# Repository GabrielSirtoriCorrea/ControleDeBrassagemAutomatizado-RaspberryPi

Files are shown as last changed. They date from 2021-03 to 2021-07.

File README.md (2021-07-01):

# Controle de Brassagem Automatizado

O Controle de Brassagem Automatizado, é um projeto desenvolvido com o objetivo de facilitar o processo de brassagem na produção de cerveja artesanal, deixando o procedimento mais automático e simples para o usuário.

## Processo de fabricação da cerveja artesanal

Antes de entendermos o funcionamento do projeto, precisamos estudar um pouco sobre as etapas do processo de fabricação de uma cerveja artesanal, e entender como cada um deles funciona.

Existem várias formas de se fazer cerveja artesanal, mas como todo alimento ou bebida, para sua produção são necessários alguns ingredientes principais:

- Malte
- Água
- Lúpulo
- Levedura

Eles são misturados de acordo com algumas etapas que podem ser entendidas pelo fluxograma abaixo:

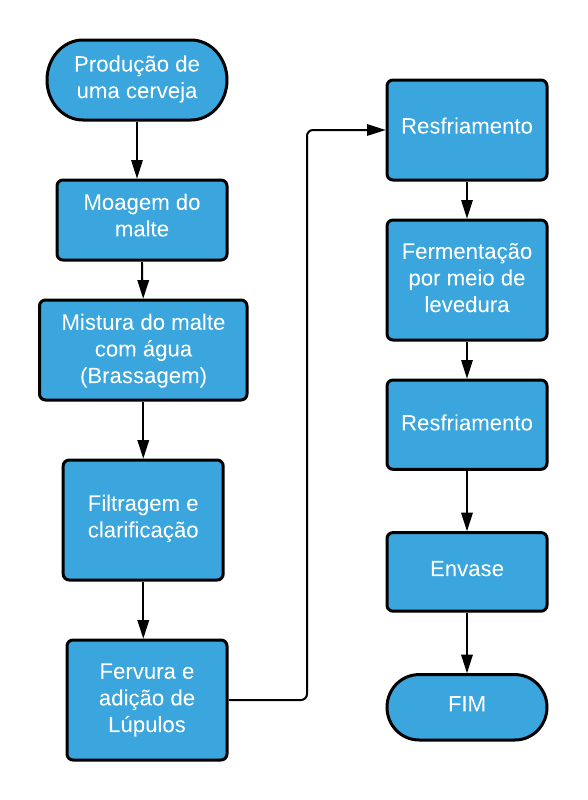
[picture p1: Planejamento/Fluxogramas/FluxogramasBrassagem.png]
Fluxograma Fabricação de cerveja
    
    
Pelo fato da fabricação da cerveja ter vários processos, nesse projeto vamos automatizar apenas 3 deles, sendo:

- Brassagem
- Filtragem e clarificação
- Fervura

Tendo isso em mente, podemos estudar um pouco mais afundo, e ver como funciona esses 3 processos de uma forma um pouco mais detalhada.

### Brassagem 

O processo de brassagem, ocorre logo após a moagem do malte, e consiste em adicionar o malte moído em uma panela de água com temperatura regulada, esse processo pode levar de 60 a 90 minutos para ser concluído, e pode ocorrer com rampas de temperatura (processo na qual o tanque mantém a temperatura em um valor determinado pelo usuário) em alguns intervalos de tempo. O fluxograma abaixo nos ajuda a compreender melhor o funcionamento desse processo:

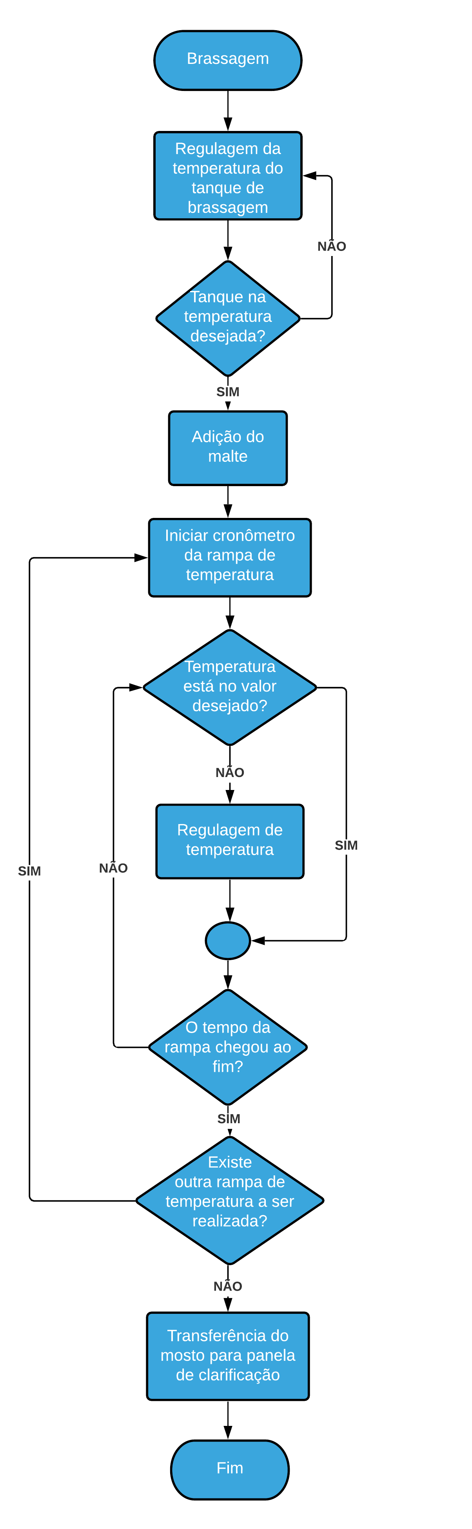
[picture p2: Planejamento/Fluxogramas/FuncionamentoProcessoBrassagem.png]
Fluxograma brassagem


### Filtragem e Clarificação

Nesse processo, o mosto (Resultado da mistura entre água e malte) é passado para uma outra panela, e começa a circular por um filtro, que será responsável por retirar as cascas dos grãos que ficaram no mosto, isso deixará a cerveja com uma coloração mais agradável e sem partículas grandes que não foram dissolvidas.

### Fervura

Após a filtragem e clarificação, entramos na etapa de fervura, essa etapa se baseia em elevar a temperatura do mosto e adicionar os Lúpulos em  alguns intervalos de tempo. Finalizada essa etapa, o mosto é levado para o processo de fermentação, o fluxograma a seguir mostra essa etapa de forma detalhada:

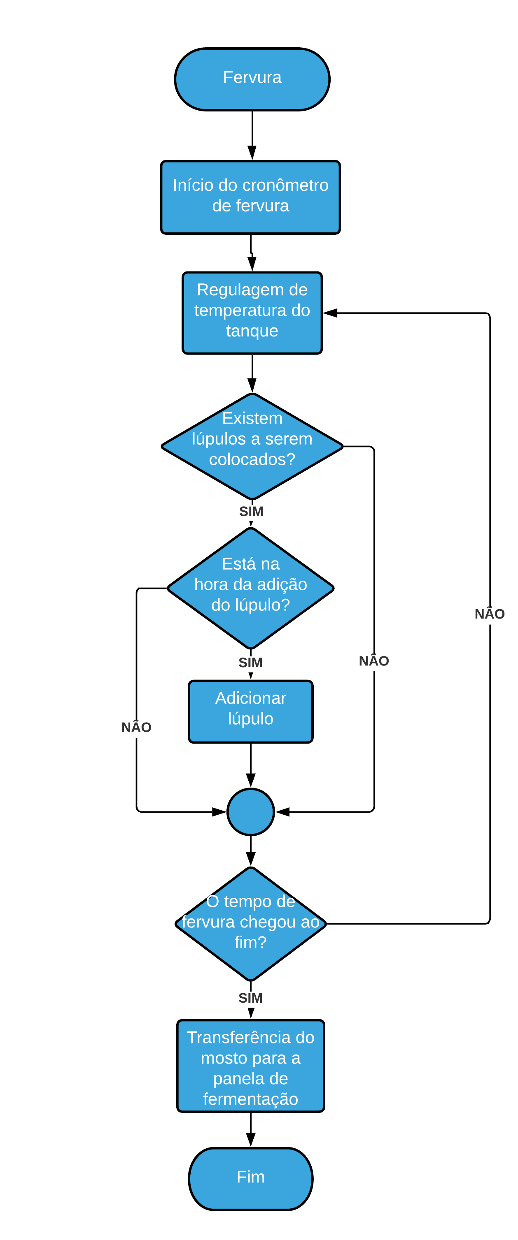
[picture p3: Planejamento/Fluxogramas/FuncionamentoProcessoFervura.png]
Fluxograma fervura


Com todos as etapas já compreendidas, podemos fazer um fluxograma completo, com todos os processos envolvidos.

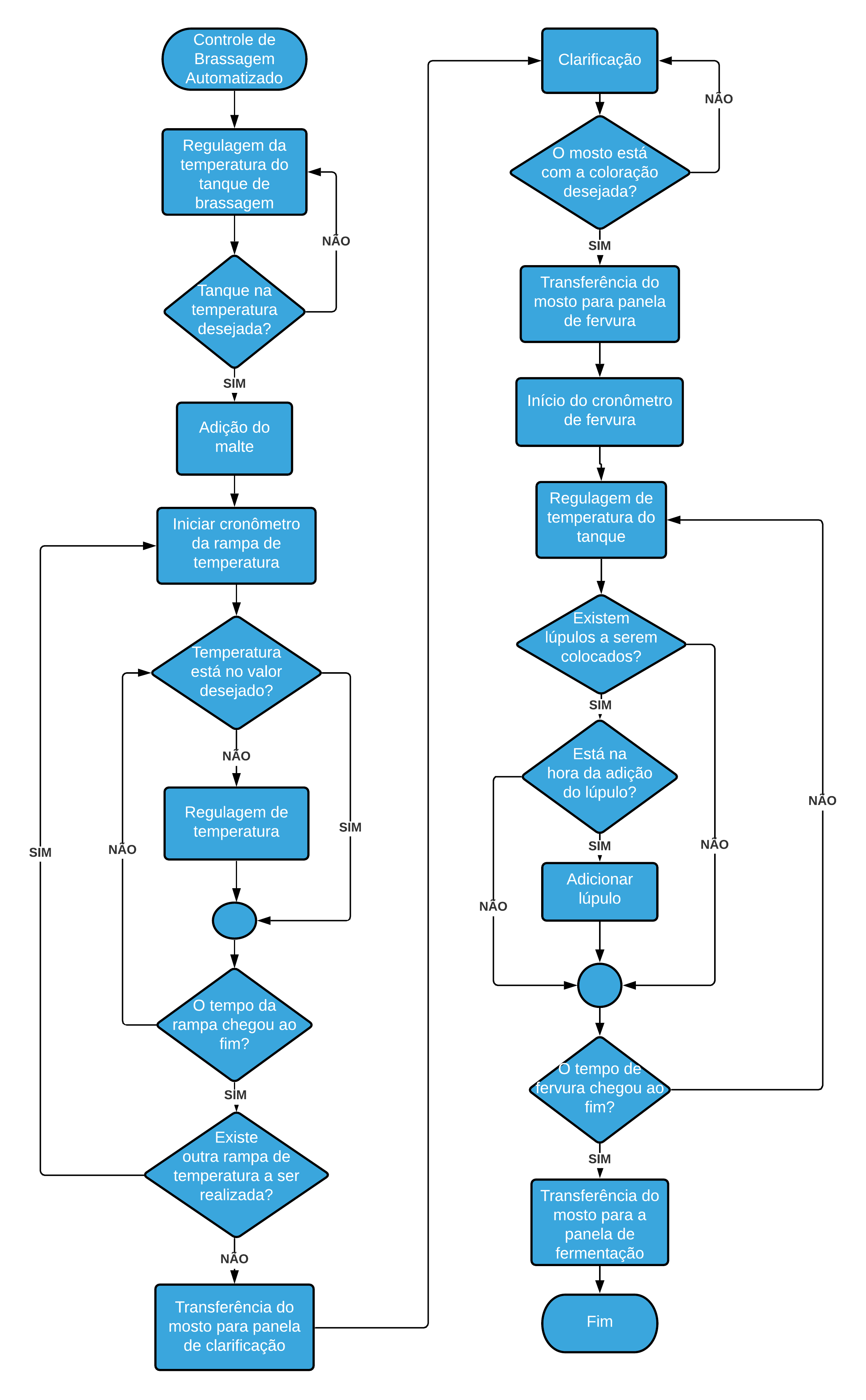
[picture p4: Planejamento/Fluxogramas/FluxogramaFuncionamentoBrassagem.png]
Fluxograma completo


Agora que conhecemos os 3 processos que serão automatizados, podemos criar uma lógica para o controle dos mesmos. Analisando as 3 etapas, podemos concluir que a principal variável existente nesses processos é a **TEMPERATURA**, que deve ser controlada na **BRASSAGEM** e **FERVURA**. Sendo assim, precisamos criar alguma estratégia para que possamos manter a **TEMPERATURA** sempre no valor que desejarmos.

## Variáveis de processo

### Controle de temperatura

A lógica de controle de temperatura consiste básicamente em 3 elementos:

- Sensor: Responsável por ler a temperatura atual do tanque
- Controlador: Responsável por receber o valor da temperatura do sensor, compará-la com o valor desejado e enviar um comando para o atuador
- Atuador: Recebe o comando do controlador, e age físicamente no processo, modificando sua temperatura

Tendo isso em mente, os dispositivos escolhidos para realizar essas funções foram:

- Sensor (TT): Sensor de temperatura DS18B20
- Controlador (TIC): Raspberry Pi com módulo ControlBeer
- Atuador (Resistência): Resistência elétrica para panela
- Relé (TY): Necessário para o acionamento da resistência

Com todos os instrumentos escolhidos, podemos criar um diagrama para auxiliar na visualização da lógica de controle de temperatura:

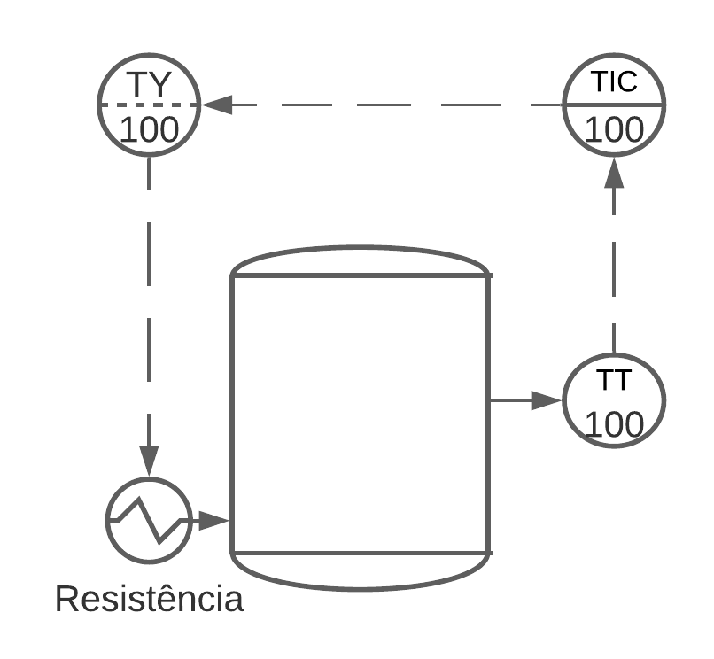
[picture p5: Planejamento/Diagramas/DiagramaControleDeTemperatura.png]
Diagrama de controle de temperatura
  

Diferentemente dos processos de brassagem e fervura, a **FILTRAGEM E CLARIFICAÇÃO**, não depende de um controle de temperatura do líquido na panela, mas sim, do seu fluxo na passagem pelo filtro, sendo assim, precisamos criar outra estratégia para que possamos transitar o mosto entre as panelas, e para realizar a passagem do líquido pelo filtro.

### Fluxo do líquido

Para realizarmos o fluxo do líquido entre as panelas, precisamos de mais alguns instrumentos, sendo eles:

- Motor: Auxilia a manter o mosto em movimento dentro da panela
- Bomba: Responsável por realizar o fluxo do líquido entre as panelas e atravéz do filtro
- Visor de vazão (FV): Necessário para analisarmos a coloração do mosto
- Válvulas de acionamento manual: Necessária para controlar o fluxo do mosto entre as panelas 

Dessa forma, o controle de fluxo do projeto será feito de acordo com o diagrama:

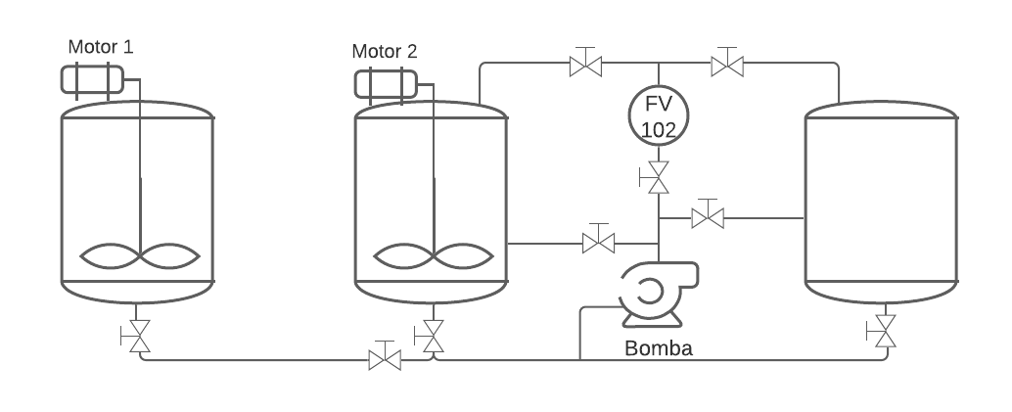
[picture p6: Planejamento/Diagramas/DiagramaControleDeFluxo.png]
Diagrama de controle de fluxo


É importante ressaltar que, devido a grande quantidade de válvulas, não é possível controla-lás eletricamente por meio de um solenoide, pois não teriamos um controlador com a quantidade de saídas necessárias, por conta disso, o usuário terá de fazer esse controle manualmente.

Agora que sabemos como será o controle das váriaveis e todos os instrumentos que iremos utilizar, podemos juntar os dois diagramas criados anteriormente e criar um diagrama final do projeto.

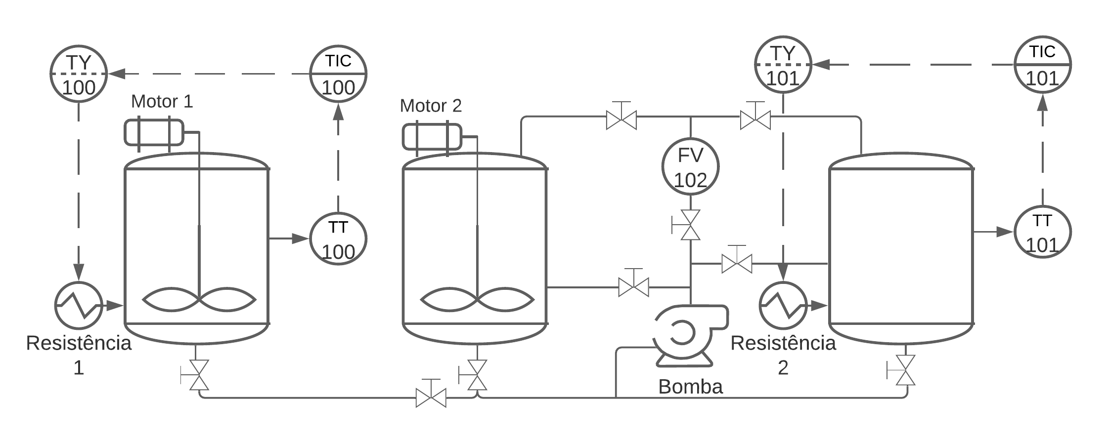
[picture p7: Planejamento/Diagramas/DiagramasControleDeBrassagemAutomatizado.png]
Diagrama final


## Componentes e ligações eletrônicas

Após identificarmos todos os instrumentos que iremos utilizar, precisamos de alguns componentes eletrônicos para que possamos acioná-los e controlá-los, sendo eles:

- Fonte 12V
- Módulo regulador de tensão 12V-5V LM2596
- Raspberry Pi 3 Model B
- 2x Sensores de temperatura DS18B20 
- 2x Resistores 4.7K Ohms
- 5x Módulos Relés
- Display Touch Nextion HDMI 1024x600

Tendo todos os componentes em mãos, podemos fazer as seguintes ligações:

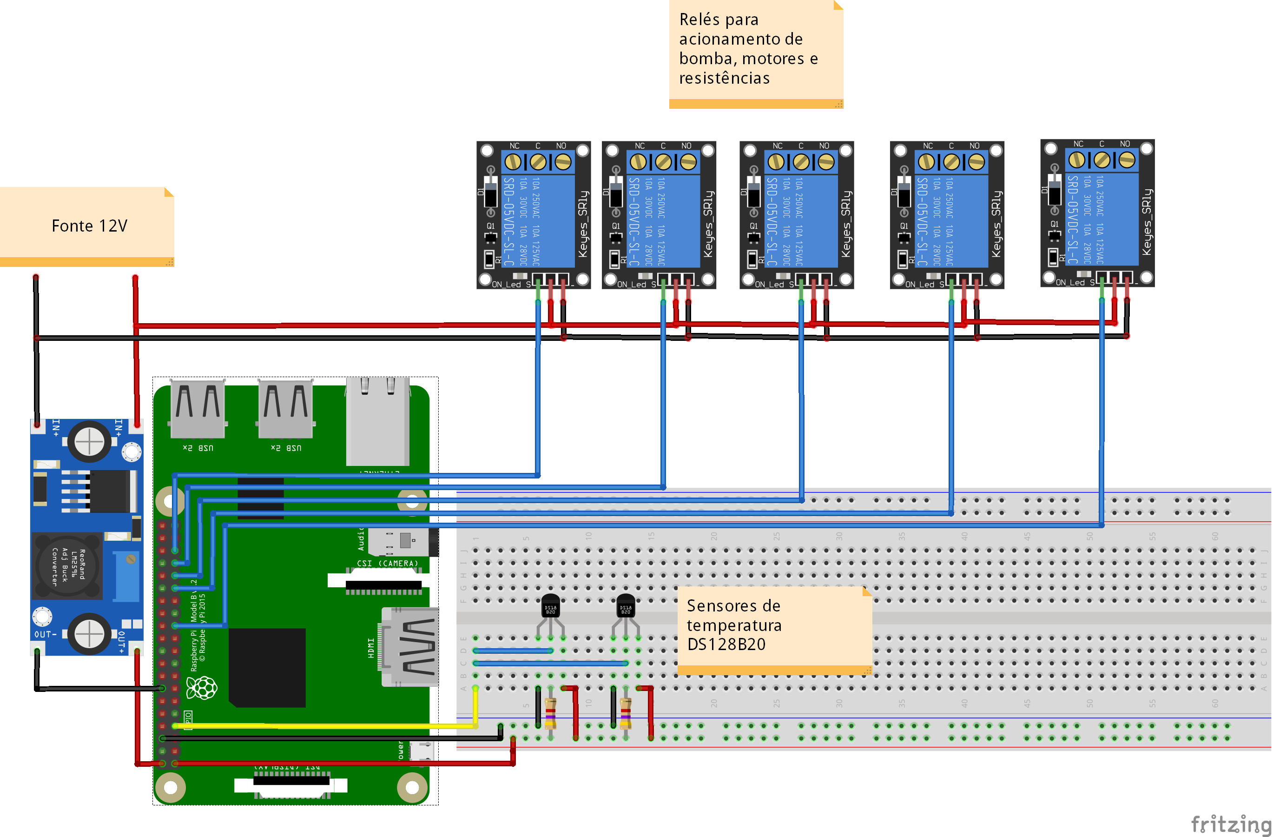
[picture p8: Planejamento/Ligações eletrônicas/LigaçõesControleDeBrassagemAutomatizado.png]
Esquema de ligações


Apesar do esquema acima ser bem simples, ele não foi utilizado no projeto, em seu lugar, foi utilizado um módulo Raspberry Pi chamado de Control Beer Pi.

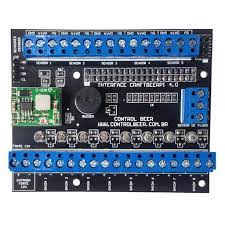
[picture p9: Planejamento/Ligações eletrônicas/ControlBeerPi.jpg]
Control Beer Pi


Esse módulo já é bem conhecido pelos cervejeiros, e nos auxilia muito por já conter um regulador de tensão 12V-5V, os resistores de 4.7k Ohms e borns para conexão, dessa forma, não precisamos de uma protoboard para fazermos a conexão.

O display nextion será a IHM do projeto, e será conectado diretamente ao Raspberry Pi por um cabo HDMI, e alimentado por um cabo USB, conectado também ao Raspberry.

## Lógica do projeto

Agora que sabemos todos os componentes que iremos utilizar, precisamos criar uma lógica para controlar todo o projeto. Para esse projeto, separamos a lógica em 3 núcleos:

- Interface: É responsável pela interação com o usuário, será exibida no IHM Nextion
- Scripts: São responsáveis pela lógica de controle de todo o sistema
- Status: Estruturado no formato JSON, é o arquivo que irá conter os estados de todos os componentes do sistema, e as configurações realizadas pelo usuário

### Interface

A Interface do projeto foi criada com a linguagem **JAVA**, juntamente com o pacote **SWING** para a criação dos Layouts. Com esse pacote importado, as classes Java podem ter um layout, dessa forma, podemos mudar o Layout da Interface apenas chamando uma outra classe. Nesse projeto, temos 4 classes Java, sendo elas:

- Interface.java: Tela inicial do sistema
- StatusController.java: Contém métodos para leitura do arquivo Status.json
- TelaBrassagemManual.java: Tela para brassagem de modo manual
- TelaNovaBrassagem.java: Tela de configuração de uma nova brassagem

#### StatusController.java

A classe StatusController é uma classe simples Java sendo a única no projeto que não utiliza o pacote Swing. Ela é responsável por **Ler e Escrever** no arquivo **Status.json**, através dos métodos **readStatus()**, **writeStatus()** e **resetStatus()**, podemos fazer isso a partir do pacote **org.json**, que foi importado para o projeto. A estrutura do arquivo **Status.json** foi criada da seguinte forma:

```
{
    "BrewStatus":"Pausado",
    "Bomb":false,
    "BrewMode":"Automatic",
    "Tank1":{
        "Ramps":[[0,0],[0,0]],
        "MaltAlert":false,
        "Temperature":0,
        "Motor":false,
        "NextProcess":false,
        "SetPoint":0,
        "ActualRamp":0,
        "Resistence":false
        },
    "Tank2":{
        "ClarificationTime":0,
        "Motor":false,
        "NextProcess":false
        },
    "Tank3":{
        "Temperature":0,
        "NextProcess":false,
        "Hops":[0,0,0],
        "BoilTime":0,
        "SetPoint":0,
        "Resistence":false,
        "HopAlert":false
        }
}
```

A implementação do método **readStatus()** é simples, só precisamos ler o arquivo Status.json com a classe **FileReader** do pocote java.io, converter para um tipo JSONObject, armazenar em uma variável e retorná-la. Essa implementação foi feita dentro de um LOOP while, isso nos permite fazer uma verificação de se a variável retornada está vazia, se ela estiver, acontece novamente a leitura. Esse tipo de erro pode ocorrer quando os scripts estiverem manipulando os dados do arquivo, dessa forma, o JSONObject não será retornado vazio, evitando um erro em outra parte do sistema.

```
public static JSONObject readStatus(){
    do{
        try {
            jsonParser = new JSONParser();
            jsonObject = new JSONObject(jsonParser.parse(new FileReader("../status.json")).toString());
        } catch (ParseException | IOException | NullPointerException e) {
            e.printStackTrace();
        }
    }while(jsonObject.isEmpty());
            
    return jsonObject;
    }
```

O método **writeStatus()** foi implementado da seguinte forma, primeiro, utilizamos o método **readStatus()** da própria classe para lermos os estados atuais de Status.json e armazená-los em uma variável do tipo JSONObject, podendo assim manipular o JSON através do método **put()**. Após isso, criamos um objeto da classe **FileWriter**, contida no pacote java.io, e escrevemos o JSONObject no arquivo Status.json, através do método **write()**. É importante ressaltar também que foi utilizado um polimorfismo em **writeStatus()**, para que possamos escrever no JSON um objeto qualquer ou um JSONArray. Além disso, colocamos uma verificação do parâmetro tank em ambos os métodos, isso nos permite mudar as variáveis de um tanque, ou do projeto como um todo.

```
public static void writeStatus(String  tank, String target, Object value){
    try {
        if(tank != null){
            originalJson = readStatus();
            jsonObject = readStatus().getJSONObject(tank);
            jsonObject.put(target, value);
            originalJson.put(tank, jsonObject);
            System.out.println(jsonObject);
            writer = new FileWriter("../status.json");
                
            writer.write(originalJson.toString());
        }else{
            jsonObject = readStatus();
            writer = new FileWriter("../status.json");
            System.out.println(jsonObject);
            jsonObject.put(target, value);
            writer.write(jsonObject.toString());
        }
            
        writer.close();
    } catch (IOException ex) {
       ex.printStackTrace();
    }
}

public static void writeStatus(String  tank, String target, JSONArray value){
    try {
        if(tank != null){
            originalJson = readStatus();
            jsonObject = readStatus().getJSONObject(tank);
            jsonObject.put(target, value);
            originalJson.put(tank, jsonObject);
            System.out.println(jsonObject);
            writer = new FileWriter("../status.json");
                
            writer.write(originalJson.toString());
        }else{
            jsonObject = readStatus();
            writer = new FileWriter("../status.json");
            System.out.println(jsonObject);
            jsonObject.put(target, value);
            writer.write(jsonObject.toString());
        }
            
        writer.close();
    } catch (IOException ex) {
        ex.printStackTrace();
    }
}
```

O método **resetStatus()** também foi implementado de forma simples, apenas criamos um novo JSONObject a partir de uma String que contém todos os valores do JSON setado em 0 ou false, a partir disso, escrevemos no Arquivo utilizando o **FileWriter** novamente 

```
public static void resetStatus(){
    try { 
        jsonObject = new JSONObject("{\"BrewStatus\":\"Pausado\",\"Tank3\":{\"Temperature\":0,\"NextProcess\":false,\"Hops\":[0,0,0],\"BoilTime\":0,\"SetPoint\":0,\"Resistence\":false,\"HopAlert\":false},\"Tank2\":{\"ClarificationTime\":0,\"Motor\":false,\"NextProcess\":false},\"BrewMode\":\"Automatic\",\"Tank1\":{\"Ramps\":[[0,0],[0,0]],\"MaltAlert\":false,\"Temperature\":0,\"Motor\":false,\"NextProcess\":false,\"SetPoint\":0,\"ActualRamp\":0,\"Resistence\":false},\"Bomb\":false}");

        writer = new FileWriter("../status.json");
        writer.write(jsonObject.toString());
        writer.close();
    } catch (IOException ex) {
        Logger.getLogger(StatusController.class.getName()).log(Level.SEVERE, null, ex);
    }
        
}
```

#### Interface.java

O layout da tela inicial foi criado da seguinte forma:

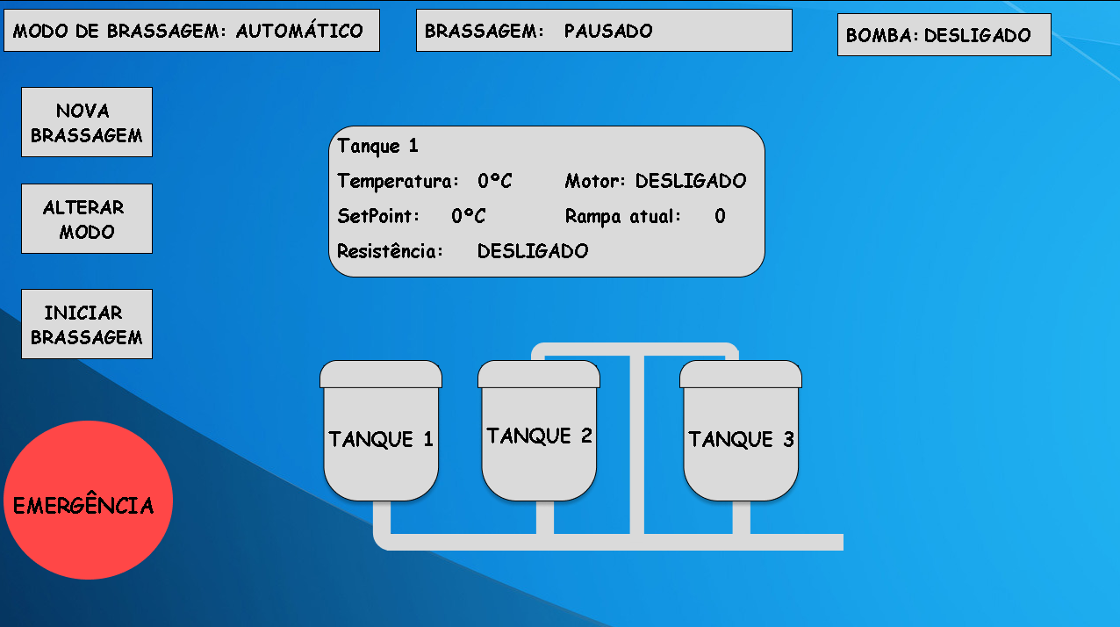
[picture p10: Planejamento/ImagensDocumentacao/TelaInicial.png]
TelaInicial


Para essa tela temos alguns componentes que são manipulados pela classe, são eles:

- Labels:

   - lblBomb: Mostra o estado da bomba
   - lblBrewStatus: Mostra o estado da brassagem (Pausado ou Em andamento)
   - lblParameter: Mostra a variável do tanque que está sendo exibida
   - lblResult: Mostra o valor da variável do tanque
   - lblStartStop: Muda o nome do botão btnStartBrew para INICIAR BRASSAGEM ou PAUSAR BRASSAGEM
   - lblTankNumber: Mostra qual é o tanque na qual as variáveis estão sendo exibidas

- Botões:

   - btnChangeMode: Chama a classe TelaBrassagemManual
   - btnEmergency: Reseta todas as variáveis do arquivo Status.json.
   - btnNewBrew: Chama a classe TelaNovaBrassagem
   - btnStartBrew: Inicia a lógica do projeto
   - btnTank1: Mostra os valores das váriaveis do tanque 1 nos labels lblResults
   - btnTank2: Mostra os valores das váriaveis do tanque 2 nos labels lblResults 
   - btnTank3: Mostra os valores das váriaveis do tanque 3 nos labels lblResults

Com todos os Botões e Labels já adicionados, precisamos implementar os métodos de cada botão para que as funções possam ser executadas quando pressionados.

Para os botões **btnChangeMode** e **btnNewBrew** foram adicionadas apenas funções que chamam uma outra classe, abaixo temos um exemplo dessa implementação:

```
private void btnNewBrewActionPerformed(java.awt.event.ActionEvent evt){                                           
    new TelaNovaBrassagem().setVisible(true);
    dispose();
    }
```

Nos botões **btnTank1**, **btnTank2**, **btnTank3** apenas mudamos o valor da variável **tankControled**, ela é responsável por armazenar o valor do tanque na qual as variáveis estão sendo exibidas na tela.

```
private void btnTank1ActionPerformed(java.awt.event.ActionEvent evt) {
    tankControled = 1;
}
```

No botão **btnEmergency**, chamamos o método **resetStatus()** da classe StatusController, dessa forma, todos os valores contidos em Status.json são resetados.

```
private void btnEmergencyActionPerformed(java.awt.event.ActionEvent evt){  
    new StatusController().resetStatus();
}
```

No Botão **btnStartBrew** criamos um objeto da classe StatusController e com o método **writeStatus()** mudamos o valor da váriavel **BrewStatus**, contida no em Status.json, para EM ANDAMENTO ou PAUSADO, isso vai depender do valor que estava contido anteriormente.

```
private void btnStartBrewActionPerformed(java.awt.event.ActionEvent evt) {                   
    status = new StatusController();
        
    if(brewStarted){
    status.writeStatus(null, "BrewStatus", "Pausado");
    lblBrewStatus.setText("PAUSADO");
    lblStartStop.setText("<html><center> INICIAR BRASSAGEM <center></html>");
    }else{
    status.writeStatus(null, "BrewStatus", "Em andamento");
    lblBrewStatus.setText("EM ANDAMENTO");
    lblStartStop.setText("<html><center> PAUSAR BRASSAGEM <center></html>");
    }
        
    brewStarted = !brewStarted;
}
```

Agora que nós ja temos todos os componentes e implementamos os métodos de todos os botões, precisamos fazer com que eles sejam atualizados constantemente, para sabermos os valores atuais das variáveis. Para isso, foi adicionada uma nova classe dentro da classe Interface.java, sendo ela a **TankController**, essa classe implementa as funções de uma interface java, chamada **ActionListener**, que foi importada para o projeto e contém o método abstrato **actionPerformed()**, esse método permite que todas as instruções contidas nele sejam executadas em LOOP, nos permitindo atualizar as variáveis em tempo real, abaixo podemos ver um exemplo para implementação da interface java **ActionListener**.

```
class TankController implements ActionListener{
    @Override
    public void actionPerformed(ActionEvent e) {
        try {

            //Instruções a serem executadas em LOOP

        } catch (InterruptedException ex) {
            Logger.getLogger(Interface.class.getName()).log(Level.SEVERE, null, ex);
        }
    } 
}
```

Podemos agora implementar a função actionPerformed() com tudo que queremos executar em loop no nosso sistema. No nosso caso, vamos fazer a verificação da variável **tankControled**, e mostrar os valores das variáveis do tanque correspondente, além de verificar as variáveis **Alert** em Status.json, para que possamos mostrar um alerta na tela, avisando ao usuário que uma etapa da produção foi finalizada.

```
class TankController implements ActionListener{
    @Override
    public void actionPerformed(ActionEvent e) {
        try {
            Thread.currentThread().sleep(1000);
            status = new StatusController();
            lblBomb.setText(booleanStatus(status.readStatus().getBoolean("Bomb")));

            if(status.readStatus().getJSONObject("Tank1").getBoolean("MaltAlert")){   //Verificação dos alertas
                JOptionPane.showMessageDialog(null, "ADICIONE O MALTE NA PANELA DE MOSTURAÇÃO!!!", "ATENÇÃO!!!", JOptionPane.WARNING_MESSAGE);
            }
            if(status.readStatus().getJSONObject("Tank3").getBoolean("HopAlert")){
                JOptionPane.showMessageDialog(null, "ADICIONE O LÚPULO NA PANELA DE FERVURA!!!", "ATENÇÃO!!!", JOptionPane.WARNING_MESSAGE);
            }
            if(status.readStatus().getJSONObject("Tank1").getBoolean("NextProcess")){
                JOptionPane.showMessageDialog(null, "ACIONE AS VÁVULAS PARA O PROCESSO DE CLARIFICAÇÃO!!!", "ATENÇÃO!!!", JOptionPane.WARNING_MESSAGE);
            }
            if(status.readStatus().getJSONObject("Tank2").getBoolean("NextProcess")){
                JOptionPane.showMessageDialog(null, "ACIONE AS VÁVULAS PARA O PROCESSO DE FERVURA!!!", "ATENÇÃO!!!", JOptionPane.WARNING_MESSAGE);
            }
            if(status.readStatus().getJSONObject("Tank3").getBoolean("NextProcess")){
                JOptionPane.showMessageDialog(null, "ACIONE AS VÁVULAS PARA O PROCESSO DE FERMENTAÇÃO!!!", "ATENÇÃO!!!", JOptionPane.WARNING_MESSAGE);
            }

            switch(tankControled){  //Verificação do tanque na qual deve exibir as variáveis 
                case 1:
                    lblTankNumber.setText("Tanque 1");

                    lblParameter1.setText("Temperatura:");
                    lblParameter2.setText("SetPoint:");
                    lblParameter3.setText("Resistência:");
                    lblParameter4.setText("Motor:");
                    lblParameter5.setText("Rampa atual:");

                    lblResult1.setText(Integer.toString(status.readStatus().getJSONObject("Tank1").getInt("Temperature")) + "ºC");
                    lblResult2.setText(Integer.toString(status.readStatus().getJSONObject("Tank1").getInt("SetPoint")) + "ºC");
                    lblResult3.setText(booleanStatus(status.readStatus().getJSONObject("Tank1").getBoolean("Resistence")));
                    lblResult4.setText(booleanStatus(status.readStatus().getJSONObject("Tank1").getBoolean("Motor")));
                     lblResult5.setText(Integer.toString(status.readStatus().getJSONObject("Tank1").getInt("ActualRamp")));
                     break;
                case 2:
                    lblTankNumber.setText("Tanque 2");

                    lblParameter1.setText("Motor:");
                    lblParameter2.setText("");
                    lblParameter3.setText("");
                    lblParameter4.setText("");
                    lblParameter5.setText("");

                    lblResult1.setText(booleanStatus(status.readStatus().getJSONObject("Tank2").getBoolean("Motor"));
                    lblResult2.setText("");
                    lblResult3.setText("");
                    lblResult4.setText("");
                    lblResult5.setText("");
                    break;
                case 3:
                    lblTankNumber.setText("Tanque 3");

                    lblParameter1.setText("Temperatura:");
                    lblParameter2.setText("SetPoint");
                    lblParameter3.setText("Resistência:");
                    lblParameter4.setText("");
                    lblParameter5.setText("");
                    lblResult1.setText(Integer.toString(status.readStatus().getJSONObject("Tank3").getInt("Temperature")) + "ºC");
                    lblResult2.setText(Integer.toString(status.readStatus().getJSONObject("Tank3").getInt("SetPoint")) + "ºC");
                    lblResult3.setText(booleanStatus(status.readStatus().getJSONObject("Tank3").getBoolean("Resistence")));
                    lblResult4.setText("");
                    lblResult5.setText("");
                    break;
            }
        } catch (InterruptedException ex) {
            Logger.getLogger(Interface.class.getName()).log(Level.SEVERE, null, ex);
        }  
    }
    private String booleanStatus(boolean status){
        if(status) return "LIGADO";
        else return "DESLIGADO";
    }
}
```

Depois de implementarmos o método, precisamos executá-lo, para isso precisamos importar a classe **Timer** do pacote Swing, e criarmos um objeto passando como parâmetro um objeto da classe **TankController**, após isso, chamamos o método **start()**.

```
Timer timer = new Timer(1000, new TankController());
timer.start();
```

#### TelaBrassagemManual.java

A TelaBrassagemManual fornece ao usuário a opção de controlar todo o sistema manualmente, seu layout foi criado da seguinte forma:

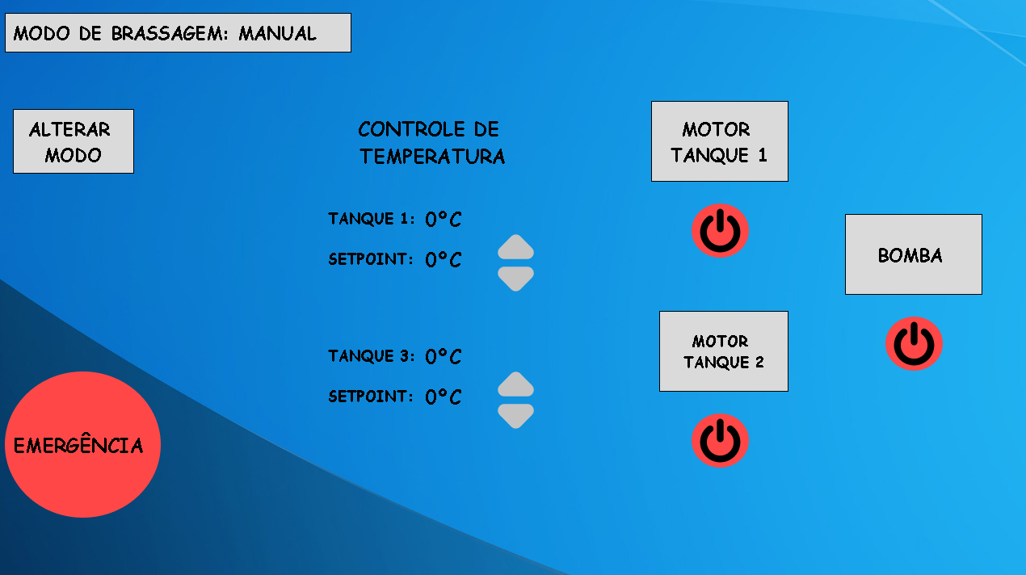
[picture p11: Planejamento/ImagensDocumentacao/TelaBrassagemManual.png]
TelaBrassagemManual


Para esse layout, temos os seguintes componentes

- Labels

    - lblSetpointTank1: Mostra o SetPoint de temperatura do tanque 1
    - lblSetPointTank3: Mostra o SetPoint de temperatura do tanque 3
    - lblTempTank1: Mostra o valor atual da temperatura do tanque 1
    - lblTempTank3: Mostra o valor atual da temperatura do tanque 3
    - ledBomb: Mostra o estado da bomba
    - ledMotorTank1: Mostra o estado do motor do tanque 1
    - ledMotorTank2: Mostra o estado do motor do tanque 2

- Botões

    - btnAdSetpointTank1: Adiciona +1 ao Setpoint de temperatura do tanque 1
    - btnAdSetpointTank3: Adiciona +1 ao Setpoint de temperatura do tanque 3
    - btnSubSetpointTank1: Subtrai -1 ao Setpoint de temperatura do tanque 1
    - btnSubSetpointTank3: Subtrai -1 ao Setpoint de temperatura do tanque 3
    - btnBomb: Muda o estado da bomba
    - btnChangeMode: Chama a classe TelaInicial
    - btnEmergency: Reseta todas as variáveis do arquivo Status.json 
    - btnMotorTank1: Muda o estado do motor do tanque 1
    - btnMotorTank2: Muda o estado do motor do tanque 2

Para a brassagem manual, os botões **btnMotorTank1**, **btnMotorTank2** e **btnBomb** tem a função de mudar as variáveis contidas em Status.json de forma direta, então criamos uma variável para armazenar o estado de cada elemento a ser controlado, pegamos esse valor e o invertemos, depois passamos como parâmetro através do método **writeStatus()**. Para o usuário ter a informação do valor da variável, foi adicionado um ícone de ON/OFF em um label vazio, a imagem a ser exibida, depende do valor da variável.

```
private void btnBombActionPerformed(java.awt.event.ActionEvent evt) {                                        
        status = new StatusController();
        bombStatus =  !bombStatus;
        status.writeStatus(null, "Bomb", bombStatus);
        if(bombStatus){
            ledBomb.setIcon(ledON);
        }else{
            ledBomb.setIcon(ledOFF);
        }
```

Os botões **btnSubSetPointTank1**, **btnSubSetPointTank3**, **btnAdSetPointTank1** e **btnAdSetPointTank3**, foram implementados com uma lógica semelhante a dos botões citados anteriormente, sua única diferença é a de adicionar +1 ou subtrair -1 ao valor lido, e mostrá-lo no label correspondente.

```
private void btnAdSetpointTank1ActionPerformed(java.awt.event.ActionEvent evt) {     
        status = new StatusController();
        Tank1SetPointValue =  Tank1SetPointValue + 1;
        status.writeStatus("Tank1", "SetPoint", Tank1SetPointValue);
        lblSetpointTank1.setText(Integer.toString(Tank1SetPointValue)+"ºC");
}
```

Para podermos atualizar constantemente o valor de temperatura dos tanques, foi utilizada a mesma lógica de Interface.java, utilizando uma classe, dessa vez a TempControl,  que implementa a interface java ActionListener.

```
class TempControl implements ActionListener{
        @Override
        public void actionPerformed(ActionEvent e) {
            status = new StatusController();
            lblTempTank1.setText(Integer.toString(status.readStatus().getJSONObject("Tank1").getInt("Temperature"))+ "ºC");
            lblTempTank3.setText(Integer.toString(status.readStatus().getJSONObject("Tank3").getInt("Temperature"))+ "ºC");
        }
       
    }
```

Para os botões **btnEmergency** e **btnChangeMode** foi utilizado as mesmas funções descritas em TelaInicial.

#### TelaNovaBrassagem.java

A classe TelaNovaBrassagem é responsável por adicionar as configurações feitas pelo usuário em Status.json, contém o seguinte layout:

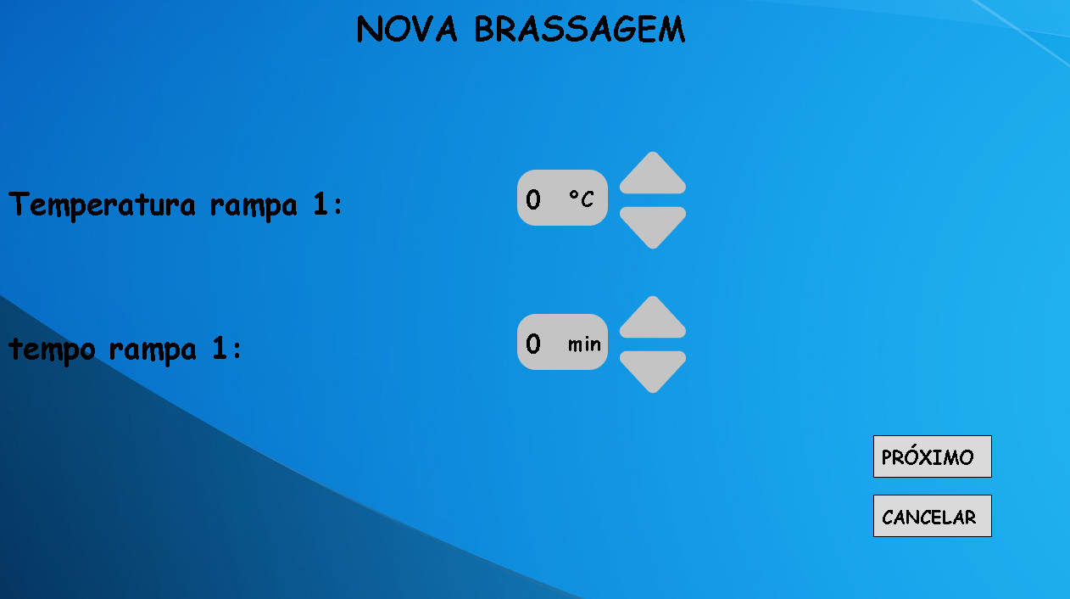
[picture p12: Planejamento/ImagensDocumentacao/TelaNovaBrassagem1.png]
TelaNovaBrassagem


E os seguintes componentes:

- Labels 
    
    - lblConfig: Mostra ao usuário qual parâmetro deve ser configurado
    - lblTarget: É o valor que o usuário deseja para o parâmetro que está configurando

- Botões

    - btnBottomArrow: Subtrai -1 ao valor que o usuário está configurando
    - btnTopArrow: Adiciona +1 ao valor que o usuário está configurando
    - btnNext: Adiciona o valor configurado ao Status.json, e muda o parâmetro a ser configurado
    - btnCancel: Chama a classe TelaInicial

Nos botões **btnBottomArrow** e **btnTopArrow** foi adicionada uma lógica para o controle da variável **targetValue**, ela é responsável por armazenar o valor que está sendo exibido em lblTarget, e o usuário a manipula através dos botões, adicionando-a ou subtraindo-a o valor 1.

```
private void btnBottomArrowActionPerformed(java.awt.event.ActionEvent evt) {   
    targetValue--;
    lblTarget.setText(Integer.toString(targetValue));
}                                              

private void btnTopArrowActionPerformed(java.awt.event.ActionEvent evt) {    
    targetValue++;
    lblTarget.setText(Integer.toString(targetValue));
}
```

É no botão **btnNext** que toda a lógica para adicionarmos os dados em Status.json está contida, para fazermos isso, utilizamos novamente os métodos **readStatus()** e **writeStatus()** contidos em StatusController. Para controlarmos qual parâmetro deve ser configurado, foi criada a variável **config**, ela armazena um valor inteiro, e através de um switch, adicionamos o valor no Status.json e mudamos os valores de lblConfig para o próximo parâmetro a ser configurado.

```
private void btnNextActionPerformed(java.awt.event.ActionEvent evt) {
    config = 0;                         //No código original, os atributos foram declarados no início
    actualRamp = 1;
    actualHop = 1;
    targetValue = 0;
    target1Value = 0;
    allRampsArray  = new JSONArray();
    allHopsArray  = new JSONArray();
    actualRampArray = new JSONArray();

    status = new StatusController();
        
    switch(config){
        case 0:
            status.writeStatus("Tank1", "SetPoint", targetValue);
            lblConfig.setText("Quantidade de rampas: ");
            lblUnidTarget.setVisible(false);
            setTargetsValues(0,0);
            config++;
            break;
        case 1:
            rampsNumber =  targetValue;
            lblConfig.setText("Temperatura rampa 1:");
            lblUnidTarget.setVisible(true);
            lblConfig1.setText("tempo rampa 1:");
            setSecondConfigVisible(true);
            setTargetsValues(0,0);
            config++;
            break;
        case 2:
            actualRampArray.add(Integer.parseInt(lblTarget.getText()));
            actualRampArray.add(Integer.parseInt(lblTarget1.getText()));
            allRampsArray.add(actualRampArray);
            rampsNumber--;
            actualRamp++;
            lblConfig.setText("Temperatura rampa " + Integer.toString(actualRamp) + ":");
            lblConfig1.setText("tempo rampa "+ Integer.toString(actualRamp) + ":");
            setTargetsValues(0,0);
            if(rampsNumber ==  0){
                status.writeStatus("Tank1", "Ramps", allRampsArray);
                setSecondConfigVisible(false);
                lblConfig.setText("Tempo de clarificação:");
                lblUnidTarget.setText("min");
                config++;
            }
            break;
        case 3:
            status.writeStatus("Tank2", "ClarificationTime", Integer.parseInt(lblTarget.getText()));
            setTargetsValues(0,0);
            lblConfig.setText("Temperatura de fervura:");
            lblUnidTarget.setText("ºC");
            config++;
            break;
        case 4:
            status.writeStatus("Tank3", "SetPoint", Integer.parseInt(lblTarget.getText()));
            setTargetsValues(0,0);
            lblConfig.setText("Tempo de fervura:");
            lblUnidTarget.setText("min");
            config++;
            break;
        case 5:
            status.writeStatus("Tank3", "BoilTime", Integer.parseInt(lblTarget.getText()));
            setTargetsValues(0,0);
            lblConfig.setText("Quantidade de Lúpulos: ");
            lblUnidTarget.setVisible(false);
            config++;
            break;
        case 6:
            hopsNumber = targetValue;
            lblConfig.setText("Tempo do 1º Lúpulo:");
            lblUnidTarget.setVisible(true);
            setTargetsValues(0,0);
            config++;
            break;
        case 7:
            allHopsArray.add(Integer.parseInt(lblTarget.getText()));
            hopsNumber--;
            actualHop++;
            lblConfig.setText("Tempo do " + Integer.toString(actualHop) + "º  Lúpulo:");
            setTargetsValues(0,0);
            if(hopsNumber == 1){
                lblNext.setText("FINALIZAR");
            }
            if(hopsNumber == 0){
                status.writeStatus("Tank3", "Hops", allHopsArray);
                new Interface().setVisible(true);
                dispose();
            }
            break;
        case 8:
            break;
    }   
}
```

No botão **btnCancel**, apenas chamamos a classe Interface.java, como ja foi feito anteriormente em outros métodos.

### Scripts

Os Scripts são responsáveis por controlar a GPIO do Raspberry Pi, através da linguagem python, no total, existem 4 Scripts.

- BrewControler: Script principal, contém toda a lógica de funcionamento da brassagem
- GPIOController: Contém uma classe para controle da GPIO
- TemperatureSensorsController: Contém uma classe para controle dos sensores de temperatura DS18B20
- StatusController: Contém métodos para leitura do arquivo Status.json

#### StatusController.py

Nesse arquivo, temos alguns métodos para a leitura do arquivo Status.json, já explicado anteriormente, esses métodos são novamente **readStatus()**, **writeStatus()** e **resetStatus()**, eles contém a mesma lógica dos métodos contidos na classe StatusController.java da interface.

```
path = '../status.json'

def readStatus():                
    file = open(path, 'r')
    sleep(0.25)
    return json.load(file)

def writeStatus(tank, target, value):
    status = readStatus()
    sleep(0.25)
    if tank == None:
        status[target] = value
    else:
        status[tank][target] = value
    file = open(path, 'w')
    json.dump(status, file)

def resetStatus():
    defaultStatus = {'BrewStatus':'Pausado','Tank3':{'Temperature':0,'NextProcess':False,'Hops':[0,0,0],'BoilTime':0,'SetPoint':0,'Resistence':False,'HopAlert':False},'Tank2':{'ClarificationTime':0,'Motor':False,'NextProcess':False},'BrewMode':'Automatic','Tank1':{'Ramps':[[0,0],[0,0]],'MaltAlert':False,'Temperature':0,'Motor':False,'NextProcess':False,'SetPoint':0,'ActualRamp':0,'Resistence':False},'Bomb':False}
    file = open(path, 'w')
    json.dump(defaultStatus, file)
    sleep(0.25)
```

#### GPIOController.py

Para controlarmos a GPIO do Raspberry Pi, precisamos importar para esse arquivo, a classe GPIO, contida na biblioteca Rpi, e a classe Buzzer da biblioteca gpiozero, para controlarmos o buzzer de maneira mais simples. Após isso criamos a classe **GPIOController**, no método construtor declaramos atributos para cada saída da GPIO que queremos controlar, e setamos cada uma delas como OUTPUT.

```
class GPIOController:
    def __init__(self):
        self.BOMB = 19
        self.MOTOR_1 = 13
        self.MOTOR_2 = 6
        self.RESISTENCE_1 = 5
        self.RESISTENCE_2 = 11
        self.BUZZER = 22

        GPIO.cleanup()
        os.system('modprobe w1-gpio')
        os.system('modprobe w1-therm')
        GPIO.setmode(GPIO.BCM)

        GPIO.setup(self.BOMB, GPIO.OUT)
        GPIO.setup(self.MOTOR_1, GPIO.OUT)
        GPIO.setup(self.MOTOR_2, GPIO.OUT)
        GPIO.setup(self.RESISTENCE_1, GPIO.OUT)
        GPIO.setup(self.RESISTENCE_2, GPIO.OUT)
        self.buzzer = Buzzer(self.BUZZER)
```

Após isso, implementamos os métodos Getters e Setters para cada saída, e pedimos como parâmetro um valor booleano e setamos a saída com True como HIGH e False como LOW, abaixo temos um exemplo dessa implementação

```
def setBomb(self, value):
        if value == True:
            GPIO.output(self.BOMB, GPIO.HIGH)
        else:
            GPIO.output(self.BOMB, GPIO.LOW)
```

O método para controle do Buzzer é um pouco diferente, pois temos a biblioteca, que nos permite apenas ligá-lo ou desligado, dessa forma, pedimos como parâmetro apenas o tempo em que o buzzer deve permanecer ligado

```
def buzzerBeep(self, secs):
        self.buzzer.on()
        sleep(secs)
        self.buzzer.off()
```

#### TemperatureSensorsController.py

Para fazermos o controle de temperatura do nosso sistema, precisamos ler o sensor DS18B20 através da comunicação OneWire, o sensor cria no Raspberry Pi, um arquivo no diretório **/sys/bus/w1/devices/**, precisamos então ler esse arquivo, apesar de parecer simples, é necessário fazer algumas configurações no Raspberry Pi, você pode aprender a fazer essas configurações no tutorial do link abaixo:

https://labprototipando.com.br/2020/06/22/como-utilizar-o-sensor-de-temperatura-ds18b20-no-raspberry-pi/

Com o Raspberry Pi configurado, podemos criar uma classe para a leitura do arquivo criado, e colocamos em seu construtor o diretório do arquivo, no nosso caso temos dois sensores, sendo assim 2 arquivos são criado em pastas diferentes. Utilizamos as bibliotecas **glob** e **os** para nos ajudar a encontrar os diretórios dos arquivos.

```
class TemperatureSensors:
    def __init__(self):
        os.system('modprobe w1-gpio')
        os.system('modprobe w1-therm')

        self.SENSORS_BASE_DIR = '/sys/bus/w1/devices/'

        self.DEVICE_1_FOLDER = glob.glob(self.SENSORS_BASE_DIR + '28*')[0]
        self.DEVICE_1_FILE = self.DEVICE_1_FOLDER + '/w1_slave'

        self.DEVICE_2_FOLDER = glob.glob(self.SENSORS_BASE_DIR + '28*')[1]
        self.DEVICE_2_FILE = self.DEVICE_2_FOLDER + '/w1_slave'
```

Tendo os diretórios dos arquivos, podemos ler, filtrar as informações irrelevantes, e retornar a temperatura lida como um número inteiro.

```
def getTank1Sensor(self):
        try:
            f = open(self.DEVICE_1_FILE, 'r')
            lines = f.readlines()
            f.close()
            address, temp = lines[1].split('t=')
        except:
            pass

        return round(int(temp)/1000,1)
```

#### BrewController.py

O Arquivo BrewController.py é o principal do sistema, é nele que está contida toda a lógica de funcionamento do projeto, e é o arquivo que deve ser executado pelo usuário. Esse arquivo executa 2 Threads de processamento, através da classe **Thread** da biblioteca **Threading**, sendo elas:

- startInterface: Inicia a interface do projeto
- statusSync: Coloca os estados da saída da GPIO de acordo com os estados contidos em Status.json
- brew: Contem a lógica de funcionamento do projeto

Cada thread corresponde a um método do arquivo, e conseguimos executá-las da seguinte forma:

```
Thread(target=statusSync).start()
Thread(target=brew).start()
```

Com isso, os 2 métodos serão executados em paralelo, melhorando o desempenho do projeto.

Na thread **statusSync**, nós setamos todas as saídas da GPIO, através da classe GPIOController, de acordo com os valores contidos em Status.json, além de adicionar ao JSON a temperatura atual de cada tanque. Também foi implementado nessa Thread, a lógica para o **controle de temperatura** no **modo manual**. 

```
def statusSync():
    tempTank1, tempTank3, lastTempTank1, lastTempTank3 = (0,0,0,0)
    while True:
        try:
            tempTank1 = int(temperatureSensors.getTank1Sensor())
            tempTank3 = int(temperatureSensors.getTank3Sensor())
            if tempTank1 != lastTempTank1:
                StatusController.writeStatus('Tank1', 'Temperature', temperatureSensors.getTank1Sensor())
            
            if tempTank3 != lastTempTank3:
                StatusController.writeStatus('Tank3', 'Temperature', temperatureSensors.getTank3Sensor())

            lastTempTank1 = tempTank1
            lastTempTank3 = tempTank3

            gpioController.setBomb(StatusController.readStatus()['Bomb'])
            gpioController.setMotor1(StatusController.readStatus()['Tank1']['Motor'])
            gpioController.setMotor2(StatusController.readStatus()['Tank2']['Motor'])
            gpioController.setResistence1(StatusController.readStatus()['Tank1']['Resistence'])
            gpioController.setResistence2(StatusController.readStatus()['Tank3']['Resistence'])

            status = StatusController.readStatus()  

            if status['BrewMode'] == 'Manual': 
                if status['Tank1']['Temperature'] < status['Tank1']['SetPoint']:
                    StatusController.writeStatus('Tank1', 'Resistence', True)
                else:
                    StatusController.writeStatus('Tank1', 'Resistence', False)

            if status['BrewMode'] == 'Manual':
                if status['Tank3']['Temperature'] < status['Tank3']['SetPoint']:
                    StatusController.writeStatus('Tank3', 'Resistence', True)
                else:
                    StatusController.writeStatus('Tank3', 'Resistence', False)
            
            print(tempTank1)
            print(tempTank3)
        except:
            pass
```

Como já mencionado anteriormente, a thread **brew()** contém a lógica de todo o sistema, e ela é baseada no fluxograma que explica o funcionamento dos 3 processos que serão automatizados, já vistos anteriormente, e vamos analisá-la por partes. Primeiramente, ela inicia um LOOP, na qual faz a verificação de BrewStatus em Status.json, se o valor retornado for igual a EM ANDAMENTO, inicia-se toda a lógica dos processos, **ligando o motor 1** e **regulando a temperatura do tanque 1** para a **adição do malte**.

```
def brew():
    gpioController.buzzerBeep(0.5)
    while True:
        try:
            sleep(1)
            print('Lendo Status')
            status =  StatusController.readStatus()
            if status['BrewStatus'] ==  'Em andamento' and status['BrewMode'] == 'Automatic':
                gpioController.buzzerBeep(0.5)
                StatusController.writeStatus('Tank1', 'Motor', True)
                print('Motor 1 ligado')
                temperature  =  status['Tank1']['Temperature']
                setPoint = status['Tank1']['SetPoint']

                while temperature < setPoint:
                    print('Setpoint')
                    StatusController.writeStatus('Tank1', 'Resistence', True)
                    temperature  =  StatusController.readStatus()['Tank1']['Temperature']
```

Com a temperatura regulada, a resistência do tanque 1 é desligada, e é setado o valor **MaltAlert** do JSON como **True**, para que a **Inteface** possa **mostrar um alerta** na tela do IHM e o usuário adicionar o malte na panela. Depois, entramos na etapa das rampas de temperatura, para isso, temos o array **Ramps** do JSON, dentro dele vamos armazenar outros arrays, que contém 2 posições, sendo a **primeira** o **SetPoint de temperatura**, e a **segunda** o **tempo da rampa** em minutos. Desse modo, podemos ler o array e armazenar em uma variável o SetPoint de temperatura, podendo assim regula-lá. Para conseguirmos executar a rampa no tempo desejado, utilizamos a função **time()** da biblioteca **time**, ela nos permite pegar o valor do tempo atual, dessa forma, podemos somá-lo com o tempo da rampa, contido na segunda posição dos arrays, e armazená-lo na variável **endTime**, assim temos o tempo em que a rampa irá finalizar, podemos então executar a rampa enquanto o valor do tempo atual **time()** for menor que o tempo de finalização da rampa **endTime**, quando o valor de **time()** for igual ou maior que **endTime**, a rampa é finalizada. 

```
                StatusController.writeStatus('Tank1', 'Resistence', False)
                gpioController.buzzerBeep(0.5)
                StatusController.writeStatus('Tank1', 'MaltAlert', True)
                print('Adicionar malte')
                sleep(0.5)
                StatusController.writeStatus('Tank1', 'MaltAlert', False)
                sleep(0.5)

                actualRamp = 1
                for malt in status['Tank1']['Ramps']:
                    gpioController.buzzerBeep(0.5)
                    print('Rampa ', actualRamp)
                    StatusController.writeStatus('Tank1', 'ActualRamp', actualRamp)
                    StatusController.writeStatus('Tank1', 'SetPoint', malt[0])
                    temperature  =  StatusController.readStatus()['Tank1']['Temperature']
                    setPoint = malt[0]
                    endTime = time() + malt[1]*60

                    while time() < endTime:
                        if temperature < setPoint:
                            StatusController.writeStatus('Tank1', 'Resistence', True)
                        else:
                            StatusController.writeStatus('Tank1', 'Resistence', False)

                        temperature = StatusController.readStatus()['Tank1']['Temperature']

                    actualRamp+=1
```

Com todas as rampas realizadas, podemos desligar a resistência e o motor 1, além de setar o valor **NextProcess** como **True**, para fazer com que a Interface mostre um alerta na tela do IHM, avisando o usuário para fazer a transição do mosto para outra panela, abrindo as válvulas necessárias. Após isso a bomba e o motor 2 são ligados e o sistema entra em um **sleep()** para a **clarificação**, o tempo de sleep será dado pelo valor contido em **ClarificationTime** no JSON, dado também em minutos e configurado pelo usuário anteriormente.

```
                StatusController.writeStatus('Tank1', 'Motor', False)
                StatusController.writeStatus('Tank1', 'Resistence', False)
                gpioController.buzzerBeep(0.5)
                StatusController.writeStatus('Tank1', 'NextProcess', True)
                StatusController.writeStatus(None, 'Bomb', True)
                print('Bomba Ligada')
                print('Proximo processo')
                sleep(0.35)
                StatusController.writeStatus('Tank1', 'NextProcess', False)

                StatusController.writeStatus('Tank2', 'Motor', True)
                print('Motor 2 ligado, Clarificação')
                sleep(StatusController.readStatus()['Tank2']['ClarificationTime']*60)
```

Finalizada a etapa de clarificação, setamos o **NextProcess** como True, avisando o usuário para fazer a transição do mosto para o tanque 3, entramos então na etapa de **fervura**. Para fazermos a fervura, precisamos ler dois tipos de dados em Status.json, o **BoilTime**, que contém o tempo de fervura, e o Array **Hops**, que contém o tempo de adição de cada lúpulo. Para controlarmos o tempo de fervura, foi utilizada a mesma lógica das rampas de temperatura no tanque 1, comparando o retorno de **time()** e comparando-o com a variável **boilTime**, resultado da soma do valor contido em **BoilTime** e **time()**. Para o tempo de cada lúpulo, lêmos um valor contido no array **hops** e somamos com o valor de **clock**, essa variável contém o tempo de início da fervura dada por **time()** no ínicio do código, após isso, comparamos esse valor, com o tempo atual, dado também por **time()**.

```
                gpioController.buzzerBeep(0.5)
                StatusController.writeStatus('Tank2', 'NextProcess', True)
                print('Proximo processo')
                sleep(0.5)
                StatusController.writeStatus('Tank2', 'NextProcess', False)
                StatusController.writeStatus('Tank2', 'Motor', False)

                status = StatusController.readStatus()
                print('status atual: ', status)
                temperature  =  status['Tank3']['Temperature']
                setPoint = status['Tank3']['SetPoint']
                boilTime = time() + (status['Tank3']['BoilTime']*60)
                clock = time()
                hops = status['Tank3']['Hops']

                while time() < boilTime:
                    print(hops)
                    if temperature < setPoint:
                        StatusController.writeStatus('Tank3', 'Resistence', True)
                    else:
                        StatusController.writeStatus('Tank3', 'Resistence', False)

                    if len(hops) != 0 and time() >= clock + (hops[0]*60):
                        hops.pop(0)
                        print('Adicionar Lupulo')
                        gpioController.buzzerBeep(0.5)
                        StatusController.writeStatus('Tank3', 'HopAlert', True)
                        sleep(0.4)
                        StatusController.writeStatus('Tank3', 'HopAlert', False)
                
                    temperature = StatusController.readStatus()['Tank3']['Temperature']
```

Com o término da fervura, avisamos o usuário novamente através de **NextProccess**, setamos **BrewStatus** como **Pausado**, **bomba** como **False** e finalizamos a brassagem.

```
                gpioController.buzzerBeep(0.5)
                StatusController.writeStatus('Tank3', 'NextProcess', True)
                print('Proximo processo')
                StatusController.writeStatus(None, 'BrewStatus', 'Pausado')
                StatusController.writeStatus(None, 'Bomb', False)
                sleep(0.5)
                StatusController.writeStatus('Tank3', 'NextProcess', False)
                sleep(15)
```

## Execução

Para podemos rodar o projeto ao dar boot no Raspberry Pi, devemos fazer algumas configurações. Precisamos primeiro, criar uma pasta **autostart** no diretório **.config**, e criarmos um arquivo **.desktop** dentro dessa pasta.

```
mkdir /home/pi/.config/autostart
nano /home/pi/.config/autostart/BrewController.desktop
```

Ao executarmos o comando **nano**, o Raspberry Pi irá abrir um editor de texto, e nele deve ser escrito o seguinte comando:

```
[Desktop Entry]
Type=Application
Name=Clock
Exec=sudo python3 /home/pi/BrewController.py
```

Note que em Exec, devemos utilizar o comando **sudo python3** juntamente com o diretório do arquivo **BrewController.py**.

Além de configurarmos o BrewController, precisamos também, iniciar a **Interface.java**, que deve ser executada junto com BrewController.py, e podemos configurá-la da mesma forma:

```
nano /home/pi/.config/autostart/BrewController.desktop
```

Dentro do arquivo:

```
[Desktop Entry]
Type=Application
Name=Clock
Exec=sudo java -jar /home/pi/Interface.jar
```

## Considerações finais

Apesar de ser um projeto muito interessante, ele ainda contém alguns defeitos, como por exemplo os logs de erros que aparecem na execução manual dos scripts, eles não interferem no processo, mas podem causar algum bug. Além disso, temos também o alto tempo de resposta ao pressionar algum botão da Interface, o que pode ser decorrente da baixa potência de processamento e de memória do Raspberry Pi 3 ou também da lógica do projeto. Em contra partida, temos alguns pontos positivos, como a simplicidade da interface, o que ajuda o usuário ao manusear o sistema.

Abaixo temos um link para o vídeo do funcionamento do projeto:
https://youtu.be/SRfJgCcL8y8

Trabalhei nesse projeto por 5 meses, não diretos, e sua realização foi muito divertida, e pude adquirir muitos conhecimetos com a realização dele. Por ser um projeto um pouco complexo, podem ter havido implementações que simplesmente não foram feitas, peço pra que se encontrar alguma delas, crie uma issue nesse repositório, ou até mesmo fazer a implementação e criar um pull request.

## Me faça uma doação!

Gostou do projeto? Me faça uma doação! Assim você me incentiva a aprender mais e criar novos projetos :smiley:

Você pode utilizar o App do seu banco para ler o QR Code abaixo, ou se preferir, utilizar minha chave pix:

:point_down::point_down:

0caf9f55-45dd-43a3-865c-70d005770ef7

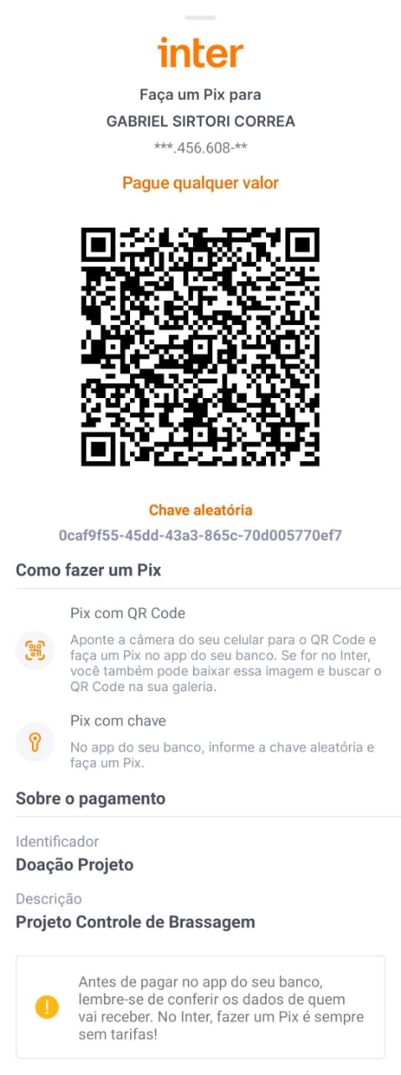
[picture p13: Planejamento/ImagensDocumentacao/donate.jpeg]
Donate


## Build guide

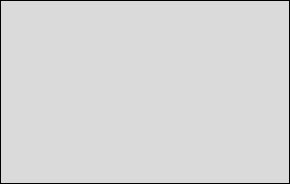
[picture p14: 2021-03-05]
Interface/build/classes/ControleDeBrassagem/Images/Rectangle 18.png

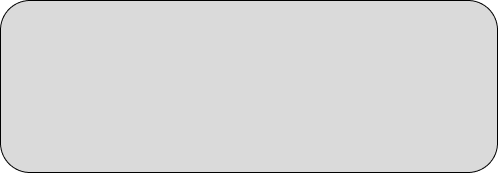
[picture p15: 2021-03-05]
Interface/build/classes/ControleDeBrassagem/Images/Rectangle 8.png

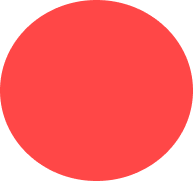
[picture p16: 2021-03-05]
Interface/build/classes/ControleDeBrassagem/Images/Ellipse 1.png

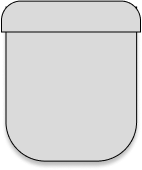
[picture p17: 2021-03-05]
Interface/build/classes/ControleDeBrassagem/Images/Group 3.png

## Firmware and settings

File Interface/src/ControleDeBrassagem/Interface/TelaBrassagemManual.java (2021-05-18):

/*
 * To change this license header, choose License Headers in Project Properties.
 * To change this template file, choose Tools | Templates
 * and open the template in the editor.
 */
package ControleDeBrassagem.Interface;

import java.awt.event.ActionEvent;
import java.awt.event.ActionListener;
import javax.swing.ImageIcon;
import javax.swing.Timer;

/**
 *
 * @author Gazebo
 */
public class TelaBrassagemManual extends javax.swing.JFrame {
    boolean newStatus;
    StatusController status;
    int newValue;
    ImageIcon ledON;
    ImageIcon ledOFF;
    boolean motor1Status = false;
    boolean motor2Status = false;
    boolean bombStatus = false; 
    int Tank1SetPointValue = 0;
    int Tank3SetPointValue = 0;
    /**
     * Creates new form TelaBrassagemManual
     */
    public TelaBrassagemManual() {
        
        this.setExtendedState(Interface.MAXIMIZED_BOTH); 
        this.setUndecorated(true);
        
        ledON = new ImageIcon(getClass().getResource("/ControleDeBrassagem/Images/BtnON.png"));
        ledOFF = new ImageIcon(getClass().getResource("/ControleDeBrassagem/Images/BtnOFF.png"));
        
        initComponents();
        status = new StatusController();
        status.resetStatus();
        status.writeStatus(null, "BrewMode", "Manual");
        
        lblSetpointTank1.setText(Integer.toString(status.readStatus().getJSONObject("Tank1").getInt("SetPoint"))+ "ºC");
        lblSetpointTank3.setText(Integer.toString(status.readStatus().getJSONObject("Tank3").getInt("SetPoint"))+ "ºC");
        
        Timer timer = new Timer(1000, new TempControl());
        timer.start();
    }

    /**
     * This method is called from within the constructor to initialize the form.
     * WARNING: Do NOT modify this code. The content of this method is always
     * regenerated by the Form Editor.
     */
    @SuppressWarnings("unchecked")
    // <editor-fold defaultstate="collapsed" desc="Generated Code">//GEN-BEGIN:initComponents
    private void initComponents() {

        jLabel3 = new javax.swing.JLabel();
        jLabel2 = new javax.swing.JLabel();
        btnEmergency = new javax.swing.JButton();
        jLabel18 = new javax.swing.JLabel();
        jLabel17 = new javax.swing.JLabel();
        jLabel5 = new javax.swing.JLabel();
        btnMotorTank2 = new javax.swing.JButton();
        jLabel4 = new javax.swing.JLabel();
        btnMotorTank1 = new javax.swing.JButton();
        ledBomb = new javax.swing.JLabel();
        jLabel8 = new javax.swing.JLabel();
        btnBomb = new javax.swing.JButton();
        ledMotorTank2 = new javax.swing.JLabel();
        ledMotorTank1 = new javax.swing.JLabel();
        jLabel14 = new javax.swing.JLabel();
        btnChangeMode = new javax.swing.JButton();
        jLabel9 = new javax.swing.JLabel();
        jLabel10 = new javax.swing.JLabel();
        jLabel11 = new javax.swing.JLabel();
        jLabel12 = new javax.swing.JLabel();
        lblSetpointTank3 = new javax.swing.JLabel();
        jLabel15 = new javax.swing.JLabel();
        lblTempTank1 = new javax.swing.JLabel();
        jLabel19 = new javax.swing.JLabel();
        jLabel20 = new javax.swing.JLabel();
        jLabel24 = new javax.swing.JLabel();
        btnSubSetpointTank3 = new javax.swing.JButton();
        btnAdSetpointTank1 = new javax.swing.JButton();
        btnSubSetpointTank1 = new javax.swing.JButton();
        jLabel23 = new javax.swing.JLabel();
        btnAdSetpointTank3 = new javax.swing.JButton();
        lblTempTank3 = new javax.swing.JLabel();
        lblSetpointTank1 = new javax.swing.JLabel();
        jLabel1 = new javax.swing.JLabel();

        setDefaultCloseOperation(javax.swing.WindowConstants.EXIT_ON_CLOSE);
        setCursor(new java.awt.Cursor(java.awt.Cursor.HAND_CURSOR));
        getContentPane().setLayout(new org.netbeans.lib.awtextra.AbsoluteLayout());

        jLabel3.setFont(new java.awt.Font("Comic Sans MS", 1, 24)); // NOI18N
        jLabel3.setText("EMERGÊNCIA");
        getContentPane().add(jLabel3, new org.netbeans.lib.awtextra.AbsoluteConstraints(20, 540, 240, 30));

        jLabel2.setIcon(new javax.swing.ImageIcon(getClass().getResource("/ControleDeBrassagem/Images/Ellipse 1.png"))); // NOI18N
        getContentPane().add(jLabel2, new org.netbeans.lib.awtextra.AbsoluteConstraints(10, 460, 200, 190));

        btnEmergency.setText("EMERGENCIA");
        btnEmergency.addActionListener(new java.awt.event.ActionListener() {
            public void actionPerformed(java.awt.event.ActionEvent evt) {
                btnEmergencyActionPerformed(evt);
            }
        });
        getContentPane().add(btnEmergency, new org.netbeans.lib.awtextra.AbsoluteConstraints(30, 510, 160, 90));

        jLabel18.setFont(new java.awt.Font("Comic Sans MS", 1, 22)); // NOI18N
        jLabel18.setText("MODO DE BRASSAGEM: MANUAL");
        getContentPane().add(jLabel18, new org.netbeans.lib.awtextra.AbsoluteConstraints(20, 20, 460, 50));

        jLabel17.setIcon(new javax.swing.ImageIcon(getClass().getResource("/ControleDeBrassagem/Images/Rectangle 9.png"))); // NOI18N
        getContentPane().add(jLabel17, new org.netbeans.lib.awtextra.AbsoluteConstraints(10, 10, 630, 70));

        jLabel5.setFont(new java.awt.Font("Comic Sans MS", 1, 22)); // NOI18N
        jLabel5.setText("<html><center>MOTOR  TANQUE 2<center></html>");
        getContentPane().add(jLabel5, new org.netbeans.lib.awtextra.AbsoluteConstraints(820, 390, 160, 100));

        btnMotorTank2.setIcon(new javax.swing.ImageIcon(getClass().getResource("/ControleDeBrassagem/Images/Rectangle 18.png"))); // NOI18N
        btnMotorTank2.setBorder(javax.swing.BorderFactory.createLineBorder(new java.awt.Color(0, 0, 0)));
        btnMotorTank2.setPreferredSize(new java.awt.Dimension(182, 32));
        btnMotorTank2.addActionListener(new java.awt.event.ActionListener() {
            public void actionPerformed(java.awt.event.ActionEvent evt) {
                btnMotorTank2ActionPerformed(evt);
            }
        });
        getContentPane().add(btnMotorTank2, new org.netbeans.lib.awtextra.AbsoluteConstraints(820, 390, 160, 100));

        jLabel4.setFont(new java.awt.Font("Comic Sans MS", 1, 22)); // NOI18N
        jLabel4.setText("<html><center>MOTOR  TANQUE 1<center></html>");
        getContentPane().add(jLabel4, new org.netbeans.lib.awtextra.AbsoluteConstraints(810, 130, 170, 100));

        btnMotorTank1.setIcon(new javax.swing.ImageIcon(getClass().getResource("/ControleDeBrassagem/Images/Rectangle 18.png"))); // NOI18N
        btnMotorTank1.setBorder(javax.swing.BorderFactory.createLineBorder(new java.awt.Color(0, 0, 0)));
        btnMotorTank1.setPreferredSize(new java.awt.Dimension(182, 32));
        btnMotorTank1.addActionListener(new java.awt.event.ActionListener() {
            public void actionPerformed(java.awt.event.ActionEvent evt) {
                btnMotorTank1ActionPerformed(evt);
            }
        });
        getContentPane().add(btnMotorTank1, new org.netbeans.lib.awtextra.AbsoluteConstraints(810, 130, 170, 100));

        ledBomb.setIcon(new javax.swing.ImageIcon(getClass().getResource("/ControleDeBrassagem/Images/BtnOFF.png"))); // NOI18N
        getContentPane().add(ledBomb, new org.netbeans.lib.awtextra.AbsoluteConstraints(1100, 390, -1, 80));

        jLabel8.setFont(new java.awt.Font("Comic Sans MS", 1, 22)); // NOI18N
        jLabel8.setText("<html><center>BOMBA<center></html>");
        getContentPane().add(jLabel8, new org.netbeans.lib.awtextra.AbsoluteConstraints(1090, 270, 140, 100));

        btnBomb.setIcon(new javax.swing.ImageIcon(getClass().getResource("/ControleDeBrassagem/Images/Rectangle 18.png"))); // NOI18N
        btnBomb.setBorder(javax.swing.BorderFactory.createLineBorder(new java.awt.Color(0, 0, 0)));
        btnBomb.addActionListener(new java.awt.event.ActionListener() {
            public void actionPerformed(java.awt.event.ActionEvent evt) {
                btnBombActionPerformed(evt);
            }
        });
        getContentPane().add(btnBomb, new org.netbeans.lib.awtextra.AbsoluteConstraints(1050, 270, 170, 100));

        ledMotorTank2.setIcon(new javax.swing.ImageIcon(getClass().getResource("/ControleDeBrassagem/Images/BtnOFF.png"))); // NOI18N
        getContentPane().add(ledMotorTank2, new org.netbeans.lib.awtextra.AbsoluteConstraints(860, 510, -1, 80));

        ledMotorTank1.setIcon(new javax.swing.ImageIcon(getClass().getResource("/ControleDeBrassagem/Images/BtnOFF.png"))); // NOI18N
        getContentPane().add(ledMotorTank1, new org.netbeans.lib.awtextra.AbsoluteConstraints(860, 250, -1, 80));

        jLabel14.setFont(new java.awt.Font("Comic Sans MS", 1, 22)); // NOI18N
        jLabel14.setText("<html><center>ALTERAR MODO<center></html>");
        getContentPane().add(jLabel14, new org.netbeans.lib.awtextra.AbsoluteConstraints(20, 140, 150, 80));

        btnChangeMode.setIcon(new javax.swing.ImageIcon(getClass().getResource("/ControleDeBrassagem/Images/Rectangle 16.png"))); // NOI18N
        btnChangeMode.setBorder(javax.swing.BorderFactory.createLineBorder(new java.awt.Color(0, 0, 0)));
        btnChangeMode.addActionListener(new java.awt.event.ActionListener() {
            public void actionPerformed(java.awt.event.ActionEvent evt) {
                btnChangeModeActionPerformed(evt);
            }
        });
        getContentPane().add(btnChangeMode, new org.netbeans.lib.awtextra.AbsoluteConstraints(20, 140, 150, 80));

        jLabel9.setFont(new java.awt.Font("Comic Sans MS", 1, 18)); // NOI18N
        jLabel9.setText("<html><center>TANQUE 3:<center></html>");
        getContentPane().add(jLabel9, new org.netbeans.lib.awtextra.AbsoluteConstraints(410, 420, 140, 50));

        jLabel10.setFont(new java.awt.Font("Comic Sans MS", 1, 24)); // NOI18N
        jLabel10.setText("<html><center>CONTROLE DE TEMPERATURA<center></html>");
        getContentPane().add(jLabel10, new org.netbeans.lib.awtextra.AbsoluteConstraints(420, 130, 240, 100));

        jLabel11.setFont(new java.awt.Font("Comic Sans MS", 1, 18)); // NOI18N
        jLabel11.setText("<html><center>SETPOINT:<center></html>");
        getContentPane().add(jLabel11, new org.netbeans.lib.awtextra.AbsoluteConstraints(410, 470, 130, 50));

        jLabel12.setFont(new java.awt.Font("Comic Sans MS", 1, 18)); // NOI18N
        jLabel12.setText("<html><center>TANQUE 1:<center></html>");
        getContentPane().add(jLabel12, new org.netbeans.lib.awtextra.AbsoluteConstraints(410, 250, 130, 50));

        lblSetpointTank3.setFont(new java.awt.Font("Comic Sans MS", 1, 24)); // NOI18N
        lblSetpointTank3.setText("<html><center>39ºC<center></html>");
        getContentPane().add(lblSetpointTank3, new org.netbeans.lib.awtextra.AbsoluteConstraints(530, 470, 90, 50));

        jLabel15.setFont(new java.awt.Font("Comic Sans MS", 1, 18)); // NOI18N
        jLabel15.setText("<html><center>SETPOINT:<center></html>");
        getContentPane().add(jLabel15, new org.netbeans.lib.awtextra.AbsoluteConstraints(410, 300, 130, 50));

        lblTempTank1.setFont(new java.awt.Font("Comic Sans MS", 1, 24)); // NOI18N
        lblTempTank1.setText("<html><center>39ºC<center></html>");
        getContentPane().add(lblTempTank1, new org.netbeans.lib.awtextra.AbsoluteConstraints(530, 250, 90, 50));

        jLabel19.setIcon(new javax.swing.ImageIcon(getClass().getResource("/ControleDeBrassagem/Images/Polygon 7.png"))); // NOI18N
        getContentPane().add(jLabel19, new org.netbeans.lib.awtextra.AbsoluteConstraints(620, 320, 50, 60));

        jLabel20.setIcon(new javax.swing.ImageIcon(getClass().getResource("/ControleDeBrassagem/Images/Polygon 6.png"))); // NOI18N
        getContentPane().add(jLabel20, new org.netbeans.lib.awtextra.AbsoluteConstraints(620, 280, 60, 60));

        jLabel24.setIcon(new javax.swing.ImageIcon(getClass().getResource("/ControleDeBrassagem/Images/Polygon 7.png"))); // NOI18N
        getContentPane().add(jLabel24, new org.netbeans.lib.awtextra.AbsoluteConstraints(620, 490, 50, 60));

        btnSubSetpointTank3.addActionListener(new java.awt.event.ActionListener() {
            public void actionPerformed(java.awt.event.ActionEvent evt) {
                btnSubSetpointTank3ActionPerformed(evt);
            }
        });
        getContentPane().add(btnSubSetpointTank3, new org.netbeans.lib.awtextra.AbsoluteConstraints(630, 510, 20, 20));

        btnAdSetpointTank1.addActionListener(new java.awt.event.ActionListener() {
            public void actionPerformed(java.awt.event.ActionEvent evt) {
                btnAdSetpointTank1ActionPerformed(evt);
            }
        });
        getContentPane().add(btnAdSetpointTank1, new org.netbeans.lib.awtextra.AbsoluteConstraints(630, 300, 20, 20));

        btnSubSetpointTank1.addActionListener(new java.awt.event.ActionListener() {
            public void actionPerformed(java.awt.event.ActionEvent evt) {
                btnSubSetpointTank1ActionPerformed(evt);
            }
        });
        getContentPane().add(btnSubSetpointTank1, new org.netbeans.lib.awtextra.AbsoluteConstraints(630, 340, 20, 20));

        jLabel23.setIcon(new javax.swing.ImageIcon(getClass().getResource("/ControleDeBrassagem/Images/Polygon 6.png"))); // NOI18N
        getContentPane().add(jLabel23, new org.netbeans.lib.awtextra.AbsoluteConstraints(620, 450, 60, 60));

        btnAdSetpointTank3.addActionListener(new java.awt.event.ActionListener() {
            public void actionPerformed(java.awt.event.ActionEvent evt) {
                btnAdSetpointTank3ActionPerformed(evt);
            }
        });
        getContentPane().add(btnAdSetpointTank3, new org.netbeans.lib.awtextra.AbsoluteConstraints(630, 470, 20, 20));

        lblTempTank3.setFont(new java.awt.Font("Comic Sans MS", 1, 24)); // NOI18N
        lblTempTank3.setText("<html><center>39ºC<center></html>");
        getContentPane().add(lblTempTank3, new org.netbeans.lib.awtextra.AbsoluteConstraints(530, 420, 90, 50));

        lblSetpointTank1.setFont(new java.awt.Font("Comic Sans MS", 1, 24)); // NOI18N
        lblSetpointTank1.setText("<html><center>39ºC<center></html>");
        getContentPane().add(lblSetpointTank1, new org.netbeans.lib.awtextra.AbsoluteConstraints(530, 300, 90, 50));

        jLabel1.setIcon(new javax.swing.ImageIcon(getClass().getResource("/ControleDeBrassagem/Images/Wallpaper.jpg"))); // NOI18N
        getContentPane().add(jLabel1, new org.netbeans.lib.awtextra.AbsoluteConstraints(0, 0, 1280, 720));

        pack();
    }// </editor-fold>//GEN-END:initComponents

    private void btnBombActionPerformed(java.awt.event.ActionEvent evt) {//GEN-FIRST:event_btnBombActionPerformed
        // TODO add your handling code here:
        status = new StatusController();
        bombStatus =  !bombStatus;
        status.writeStatus(null, "Bomb", bombStatus);
        if(bombStatus){
            ledBomb.setIcon(ledON);
        }else{
            ledBomb.setIcon(ledOFF);
        }
        
        //JOptionPane.showMessageDialog(this, "ADICIONE O MALTE NA PANELA DE MOSTURAÇÃO!!", "ERRO", JOptionPane.WARNING_MESSAGE);
    }//GEN-LAST:event_btnBombActionPerformed

    private void btnEmergencyActionPerformed(java.awt.event.ActionEvent evt) {//GEN-FIRST:event_btnEmergencyActionPerformed
        // TODO add your handling code here:
        new StatusController().resetStatus();
        lblSetpointTank1.setText("0ºC");
        lblSetpointTank3.setText("0ºC");
        ledMotorTank1.setIcon(ledOFF);
        ledMotorTank2.setIcon(ledOFF);
        ledBomb.setIcon(ledOFF);
    }//GEN-LAST:event_btnEmergencyActionPerformed

    private void btnChangeModeActionPerformed(java.awt.event.ActionEvent evt) {//GEN-FIRST:event_btnChangeModeActionPerformed
        // TODO add your handling code here:
        new StatusController().resetStatus();
        new Interface().setVisible(true);
        dispose();
    }//GEN-LAST:event_btnChangeModeActionPerformed

    private void btnSubSetpointTank3ActionPerformed(java.awt.event.ActionEvent evt) {//GEN-FIRST:event_btnSubSetpointTank3ActionPerformed
        // TODO add your handling code here:
        status = new StatusController();
        Tank3SetPointValue =  Tank3SetPointValue - 1;
        status.writeStatus("Tank3", "SetPoint", Tank3SetPointValue);
        //System.out.println(status.readStatus().getJSONObject("Tank3").getInt("SetPoint"));
        lblSetpointTank3.setText(Integer.toString(Tank3SetPointValue)+"ºC");
        
    }//GEN-LAST:event_btnSubSetpointTank3ActionPerformed

    private void btnAdSetpointTank1ActionPerformed(java.awt.event.ActionEvent evt) {//GEN-FIRST:event_btnAdSetpointTank1ActionPerformed
        // TODO add your handling code here:
        status = new StatusController();
        Tank1SetPointValue =  Tank1SetPointValue + 1;
        status.writeStatus("Tank1", "SetPoint", Tank1SetPointValue);
        //System.out.println(status.readStatus().getJSONObject("Tank1").getInt("SetPoint"));
        lblSetpointTank1.setText(Integer.toString(Tank1SetPointValue)+"ºC");
    }//GEN-LAST:event_btnAdSetpointTank1ActionPerformed

    private void btnAdSetpointTank3ActionPerformed(java.awt.event.ActionEvent evt) {//GEN-FIRST:event_btnAdSetpointTank3ActionPerformed
        // TODO add your handling code here:
        status = new StatusController();
        Tank3SetPointValue =  Tank3SetPointValue + 1;
        status.writeStatus("Tank3", "SetPoint", Tank3SetPointValue);
        //System.out.println(status.readStatus().getJSONObject("Tank3").getInt("SetPoint"));
        lblSetpointTank3.setText(Integer.toString(Tank3SetPointValue)+"ºC");
    }//GEN-LAST:event_btnAdSetpointTank3ActionPerformed
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
    public static void main(String args[]) {
        /* Set the Nimbus look and feel */
        //<editor-fold defaultstate="collapsed" desc=" Look and feel setting code (optional) ">
        /* If Nimbus (introduced in Java SE 6) is not available, stay with the default look and feel.
         * For details see http://download.oracle.com/javase/tutorial/uiswing/lookandfeel/plaf.html 
         */
        try {
            for (javax.swing.UIManager.LookAndFeelInfo info : javax.swing.UIManager.getInstalledLookAndFeels()) {
                if ("Nimbus".equals(info.getName())) {
                    javax.swing.UIManager.setLookAndFeel(info.getClassName());
                    break;
                }
            }
        } catch (ClassNotFoundException ex) {
            java.util.logging.Logger.getLogger(TelaBrassagemManual.class.getName()).log(java.util.logging.Level.SEVERE, null, ex);
        } catch (InstantiationException ex) {
            java.util.logging.Logger.getLogger(TelaBrassagemManual.class.getName()).log(java.util.logging.Level.SEVERE, null, ex);
        } catch (IllegalAccessException ex) {
            java.util.logging.Logger.getLogger(TelaBrassagemManual.class.getName()).log(java.util.logging.Level.SEVERE, null, ex);
        } catch (javax.swing.UnsupportedLookAndFeelException ex) {
            java.util.logging.Logger.getLogger(TelaBrassagemManual.class.getName()).log(java.util.logging.Level.SEVERE, null, ex);
        }
        //</editor-fold>

        /* Create and display the form */
        java.awt.EventQueue.invokeLater(new Runnable() {
            public void run() {
                new TelaBrassagemManual().setVisible(true);
            }
        });
    }

    // Variables declaration - do not modify//GEN-BEGIN:variables
    private javax.swing.JButton btnAdSetpointTank1;
    private javax.swing.JButton btnAdSetpointTank3;
    private javax.swing.JButton btnBomb;
    private javax.swing.JButton btnChangeMode;
    private javax.swing.JButton btnEmergency;
    private javax.swing.JButton btnMotorTank1;
    private javax.swing.JButton btnMotorTank2;
    private javax.swing.JButton btnSubSetpointTank1;
    private javax.swing.JButton btnSubSetpointTank3;
    private javax.swing.JLabel jLabel1;
    private javax.swing.JLabel jLabel10;
    private javax.swing.JLabel jLabel11;
    private javax.swing.JLabel jLabel12;
    private javax.swing.JLabel jLabel14;
    private javax.swing.JLabel jLabel15;
    private javax.swing.JLabel jLabel17;
    private javax.swing.JLabel jLabel18;
    private javax.swing.JLabel jLabel19;
    private javax.swing.JLabel jLabel2;
    private javax.swing.JLabel jLabel20;
    private javax.swing.JLabel jLabel23;
    private javax.swing.JLabel jLabel24;
    private javax.swing.JLabel jLabel3;
    private javax.swing.JLabel jLabel4;
    private javax.swing.JLabel jLabel5;
    private javax.swing.JLabel jLabel8;
    private javax.swing.JLabel jLabel9;
    private javax.swing.JLabel lblSetpointTank1;
    private javax.swing.JLabel lblSetpointTank3;
    private javax.swing.JLabel lblTempTank1;
    private javax.swing.JLabel lblTempTank3;
    private javax.swing.JLabel ledBomb;
    private javax.swing.JLabel ledMotorTank1;
    private javax.swing.JLabel ledMotorTank2;
    // End of variables declaration//GEN-END:variables


   class TempControl implements ActionListener{

        @Override
        public void actionPerformed(ActionEvent e) {
            status = new StatusController();
            lblTempTank1.setText(Integer.toString(status.readStatus().getJSONObject("Tank1").getInt("Temperature"))+ "ºC");
            lblTempTank3.setText(Integer.toString(status.readStatus().getJSONObject("Tank3").getInt("Temperature"))+ "ºC");
        }
       
    }
}

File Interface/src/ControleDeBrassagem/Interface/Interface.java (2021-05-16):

/*
 * To change this license header, choose License Headers in Project Properties.
 * To change this template file, choose Tools | Templates
 * and open the template in the editor.
 */
package ControleDeBrassagem.Interface;

import java.awt.event.ActionEvent;
import java.awt.event.ActionListener;
import java.util.logging.Level;
import java.util.logging.Logger;
import javax.swing.JOptionPane;
import javax.swing.Timer;

/**
 *
 * @author Gazebo
 */
public class Interface extends javax.swing.JFrame {
    StatusController status;
    int tankControled = 1;
    boolean brewStarted;
    /**
     * Creates new form Interface
     */
    public Interface() {
        this.setExtendedState(Interface.MAXIMIZED_BOTH); 
        this.setUndecorated(true);
        toFront();
        initComponents();
        brewStarted  = false;
        status = new StatusController();
        status.writeStatus(null, "BrewMode", "Automatic");
        System.out.println(status.readStatus().get("BrewMode"));
        status.writeStatus(null, "BrewStatus", "Pausado");
        Timer timer = new Timer(1000, new TankController());
        timer.start();
    }

    /**
     * This method is called from within the constructor to initialize the form.
     * WARNING: Do NOT modify this code. The content of this method is always
     * regenerated by the Form Editor.
     */
    @SuppressWarnings("unchecked")
    // <editor-fold defaultstate="collapsed" desc="Generated Code">//GEN-BEGIN:initComponents
    private void initComponents() {

        jLabel15 = new javax.swing.JLabel();
        jLabel9 = new javax.swing.JLabel();
        jLabel7 = new javax.swing.JLabel();
        jLabel3 = new javax.swing.JLabel();
        jLabel8 = new javax.swing.JLabel();
        jLabel4 = new javax.swing.JLabel();
        jLabel10 = new javax.swing.JLabel();
        jLabel6 = new javax.swing.JLabel();
        btnTank2 = new javax.swing.JButton();
        jLabel11 = new javax.swing.JLabel();
        jLabel5 = new javax.swing.JLabel();
        btnTank1 = new javax.swing.JButton();
        btnTank3 = new javax.swing.JButton();
        jLabel13 = new javax.swing.JLabel();
        lblBomb = new javax.swing.JLabel();
        jLabel20 = new javax.swing.JLabel();
        btnChangeMode = new javax.swing.JButton();
        jLabel12 = new javax.swing.JLabel();
        btnEmergency = new javax.swing.JButton();
        jLabel21 = new javax.swing.JLabel();
        lblParameter2 = new javax.swing.JLabel();
        lblParameter5 = new javax.swing.JLabel();
        lblParameter4 = new javax.swing.JLabel();
        lblResult1 = new javax.swing.JLabel();
        lblParameter3 = new javax.swing.JLabel();
        lblTankNumber = new javax.swing.JLabel();
        lblStartStop = new javax.swing.JLabel();
        lblResult2 = new javax.swing.JLabel();
        lblResult3 = new javax.swing.JLabel();
        lblResult4 = new javax.swing.JLabel();
        lblResult5 = new javax.swing.JLabel();
        lblParameter1 = new javax.swing.JLabel();
        lblBrewStatus = new javax.swing.JLabel();
        jLabel17 = new javax.swing.JLabel();
        jLabel16 = new javax.swing.JLabel();
        jLabel22 = new javax.swing.JLabel();
        btnNewBrew = new javax.swing.JButton();
        jLabel14 = new javax.swing.JLabel();
        btnStartBrew = new javax.swing.JButton();
        jLabel23 = new javax.swing.JLabel();
        jLabel18 = new javax.swing.JLabel();
        jLabel1 = new javax.swing.JLabel();

        jLabel15.setText("jLabel15");

        setDefaultCloseOperation(javax.swing.WindowConstants.EXIT_ON_CLOSE);
        setCursor(new java.awt.Cursor(java.awt.Cursor.HAND_CURSOR));
        getContentPane().setLayout(new org.netbeans.lib.awtextra.AbsoluteLayout());

        jLabel9.setFont(new java.awt.Font("Comic Sans MS", 1, 22)); // NOI18N
        jLabel9.setText("TANQUE 2");
        getContentPane().add(jLabel9, new org.netbeans.lib.awtextra.AbsoluteConstraints(560, 480, -1, -1));

        jLabel7.setFont(new java.awt.Font("Comic Sans MS", 1, 22)); // NOI18N
        jLabel7.setText("TANQUE 3");
        getContentPane().add(jLabel7, new org.netbeans.lib.awtextra.AbsoluteConstraints(790, 480, 130, 40));

        jLabel3.setFont(new java.awt.Font("Comic Sans MS", 1, 24)); // NOI18N
        jLabel3.setText("EMERGÊNCIA");
        getContentPane().add(jLabel3, new org.netbeans.lib.awtextra.AbsoluteConstraints(20, 550, 230, 50));

        jLabel8.setFont(new java.awt.Font("Comic Sans MS", 1, 22)); // NOI18N
        jLabel8.setText("TANQUE 1");
        getContentPane().add(jLabel8, new org.netbeans.lib.awtextra.AbsoluteConstraints(380, 480, 130, 40));

        jLabel4.setIcon(new javax.swing.ImageIcon(getClass().getResource("/ControleDeBrassagem/Images/Group 1.png"))); // NOI18N
        getContentPane().add(jLabel4, new org.netbeans.lib.awtextra.AbsoluteConstraints(780, 410, 140, 170));

        jLabel10.setIcon(new javax.swing.ImageIcon(getClass().getResource("/ControleDeBrassagem/Images/Group 1.png"))); // NOI18N
        getContentPane().add(jLabel10, new org.netbeans.lib.awtextra.AbsoluteConstraints(550, 410, -1, -1));

        jLabel6.setIcon(new javax.swing.ImageIcon(getClass().getResource("/ControleDeBrassagem/Images/Group 5.png"))); // NOI18N
        getContentPane().add(jLabel6, new org.netbeans.lib.awtextra.AbsoluteConstraints(630, 390, 250, 230));

        btnTank2.setBackground(new java.awt.Color(51, 102, 255));
        btnTank2.setText("BOTAO TANQUE 2");
        btnTank2.addActionListener(new java.awt.event.ActionListener() {
            public void actionPerformed(java.awt.event.ActionEvent evt) {
                btnTank2ActionPerformed(evt);
            }
        });
        getContentPane().add(btnTank2, new org.netbeans.lib.awtextra.AbsoluteConstraints(570, 420, 100, 140));

        jLabel11.setIcon(new javax.swing.ImageIcon(getClass().getResource("/ControleDeBrassagem/Images/Group 1.png"))); // NOI18N
        getContentPane().add(jLabel11, new org.netbeans.lib.awtextra.AbsoluteConstraints(370, 410, -1, -1));

        jLabel5.setIcon(new javax.swing.ImageIcon(getClass().getResource("/ControleDeBrassagem/Images/Group 4.png"))); // NOI18N
        getContentPane().add(jLabel5, new org.netbeans.lib.awtextra.AbsoluteConstraints(430, 520, 990, 140));

        btnTank1.setBackground(new java.awt.Color(51, 102, 255));
        btnTank1.setText("BOTAO TANQUE 1");
        btnTank1.addActionListener(new java.awt.event.ActionListener() {
            public void actionPerformed(java.awt.event.ActionEvent evt) {
                btnTank1ActionPerformed(evt);
            }
        });
        getContentPane().add(btnTank1, new org.netbeans.lib.awtextra.AbsoluteConstraints(380, 420, 120, 130));
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
